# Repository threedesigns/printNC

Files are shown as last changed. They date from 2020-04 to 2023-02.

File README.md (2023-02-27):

# printNC V2.1 (outdated) Please use [printNC Wiki](https://wiki.printnc.info/en/home) for updated files and build guide. 
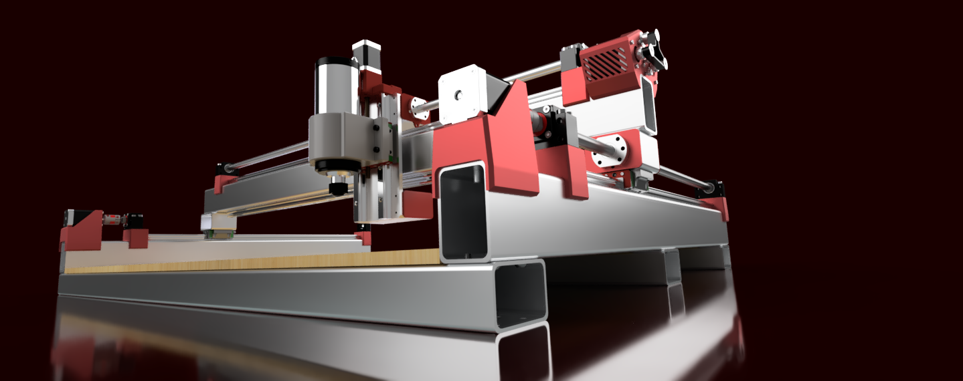
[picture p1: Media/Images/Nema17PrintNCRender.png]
printNC Logo


The PrintNC is a high-performance, DIY CNC router. It's based on a steel frame to ensure rigidity and uses 3D printed parts to make assembly easy. The PrintNC project is in active development and encourages participation.

We are looking at possibly using this repository to maintain just the models, but for now this repository should not be used.

Is there something you’re looking for that is not here yet? Join [Discord](https://discord.gg/RxzPna6) and ask there. Answers are fast and the community is quickly growing!

Additional information can also be found on the official website: [https://threedesign.store](https://threedesign.store)

## License

The PrintNC is completely open-source and operates under the CC BY 4.0 license. See the [LICENSE](LICENSE.md) file for more information.

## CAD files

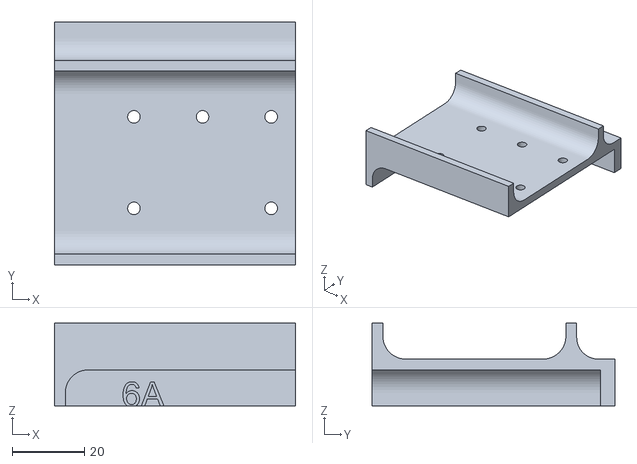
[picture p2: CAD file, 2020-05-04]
Printed Parts/Bundles/3x2x1_8 1_4 radius/Assembly Tools/6A - X Gantry Part 2.stl
66.9 x 67.4 x 23.0

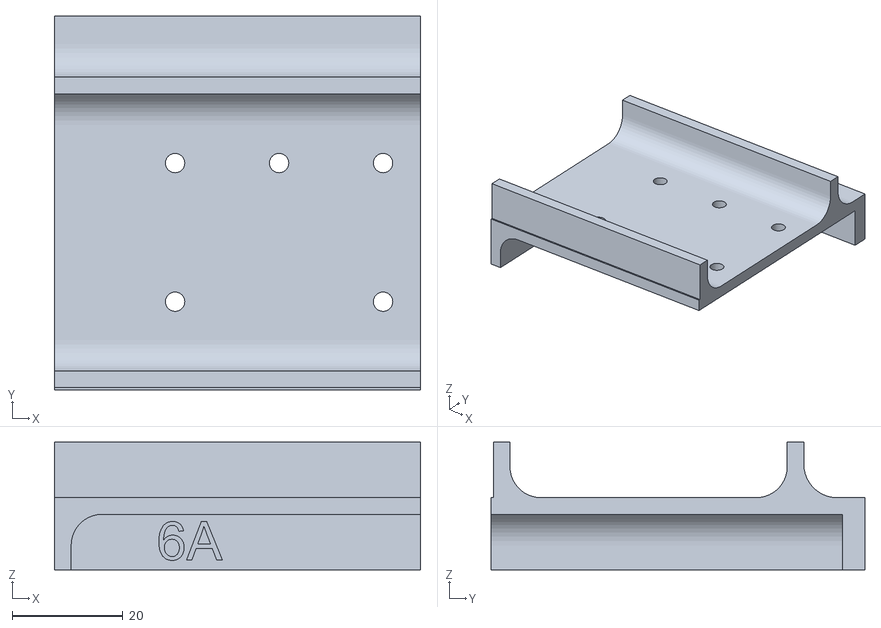
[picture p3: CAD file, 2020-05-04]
Printed Parts/Bundles/75x50x3 6mm Radius/Assembly Tools/6A - X Gantry Part 2.stl
66.0 x 67.4 x 23.0

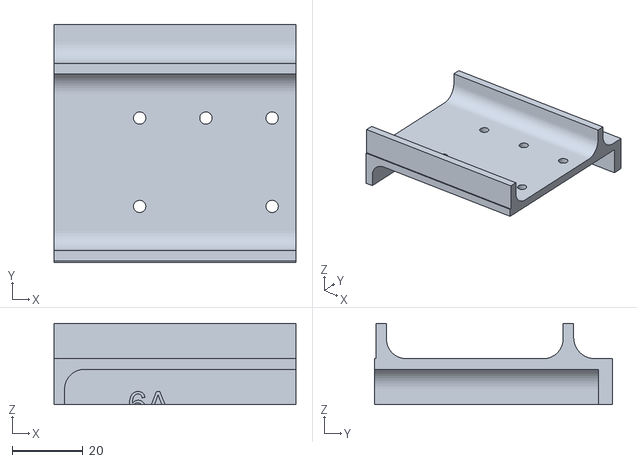
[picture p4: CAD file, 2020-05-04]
Printed Parts/Bundles/80x50x3 6mm Radius/Assembly Tools/6A - X Gantry Part 2.stl
68.5 x 67.4 x 23.0

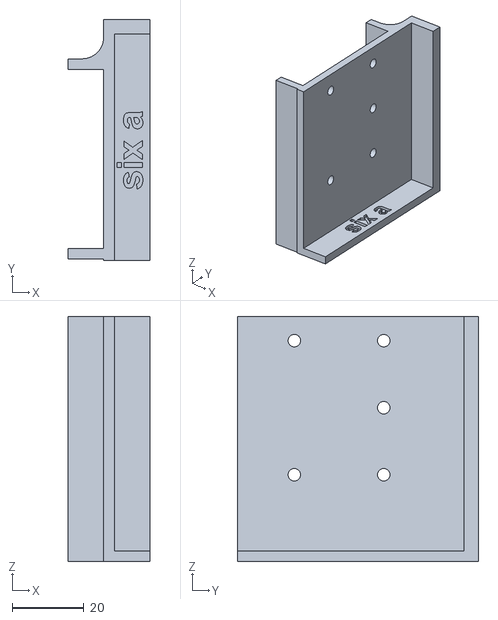
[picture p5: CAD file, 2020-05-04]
Printed Parts/Bundles/80x50x3 Square/Assembly Tools/6A - X Gantry Part 2.stl
23.0 x 67.4 x 68.5

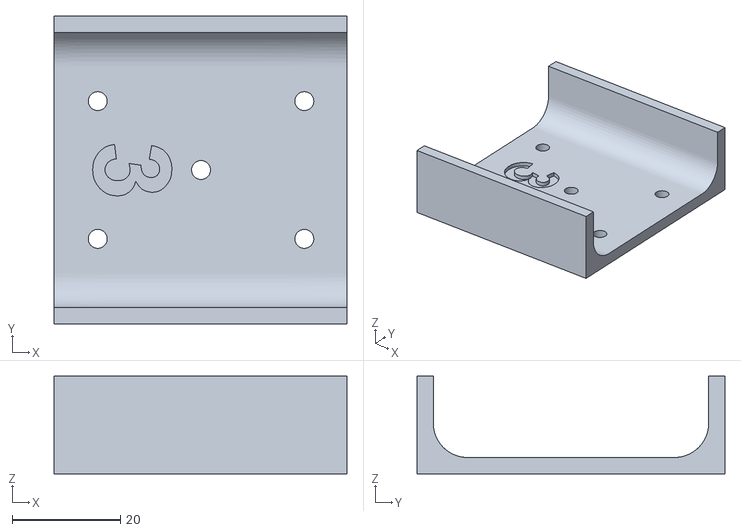
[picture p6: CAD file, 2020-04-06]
Printed Parts/Bundles/3x2x1_8 1_4 radius/Assembly Tools/3 - Y Frame Mid Marker.stl
54.0 x 56.8 x 18.0

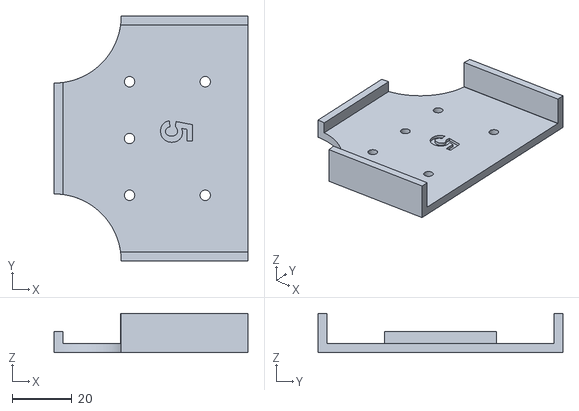
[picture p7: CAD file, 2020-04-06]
Printed Parts/Bundles/3x2x1_8 Square/Assembly Tools/5 - Y Roller Top.stl
65.0 x 82.2 x 13.1

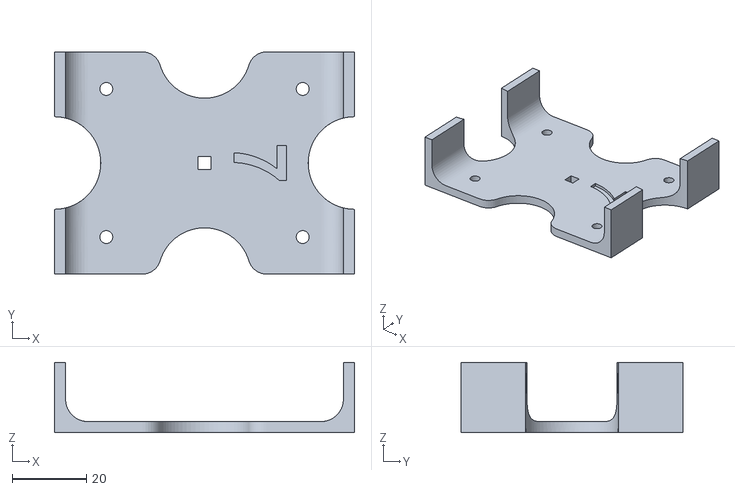
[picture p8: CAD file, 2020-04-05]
Printed Parts/Bundles/75x50x3 6mm Radius/Assembly Tools/7 - X Axis Roller.stl
81.0 x 60.0 x 19.0

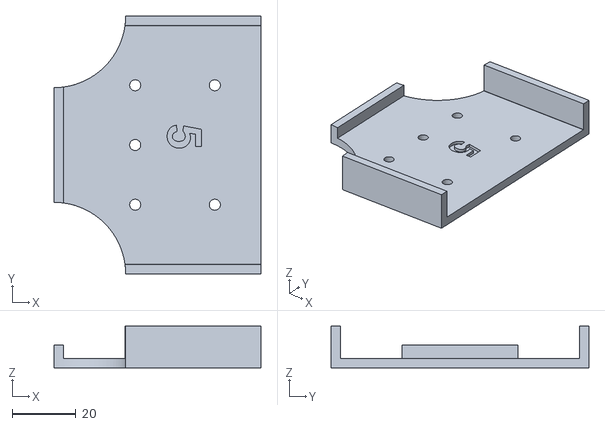
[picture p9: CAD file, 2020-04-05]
Printed Parts/Bundles/75x50x3 Square/Assembly Tools/5 - Y Roller Top.stl
65.0 x 81.0 x 13.1

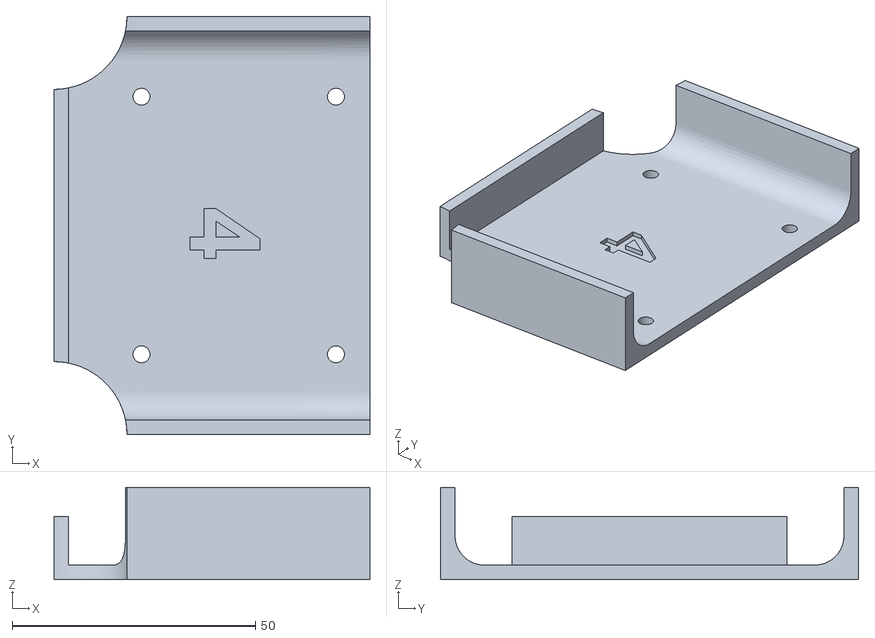
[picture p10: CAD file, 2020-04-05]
Printed Parts/Bundles/80x50x3 6mm Radius/Assembly Tools/4 - Y Roller Bottom.stl
65.0 x 86.0 x 19.0

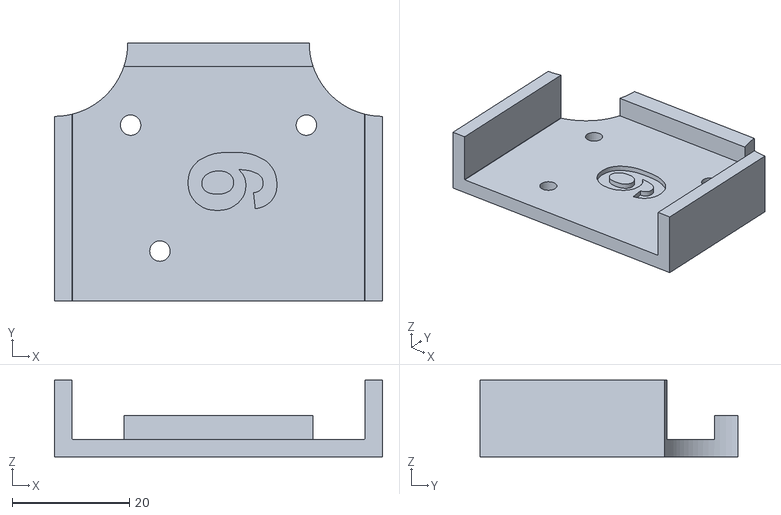
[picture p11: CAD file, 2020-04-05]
Printed Parts/Bundles/80x50x3 Square/Assembly Tools/9 - Z Face Rail Bottom.stl
56.0 x 44.0 x 13.1

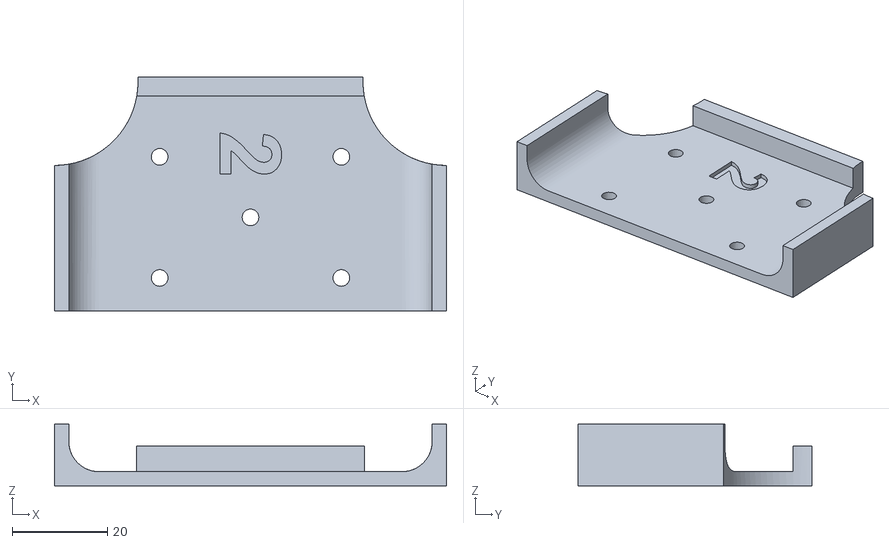
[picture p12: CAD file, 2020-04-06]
Printed Parts/Bundles/3x2x1_8 1_4 radius/Assembly Tools/2 - X Frame Marker.stl
82.2 x 49.0 x 13.0

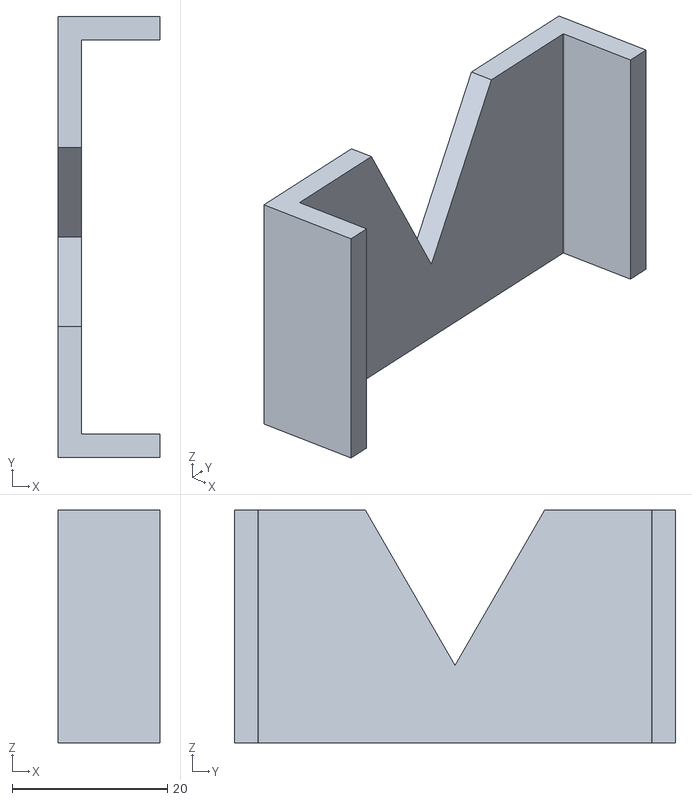
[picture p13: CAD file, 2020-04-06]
Printed Parts/Bundles/3x2x1_8 Square/Assembly Tools/Centre Line Marker.stl
13.1 x 56.8 x 30.0

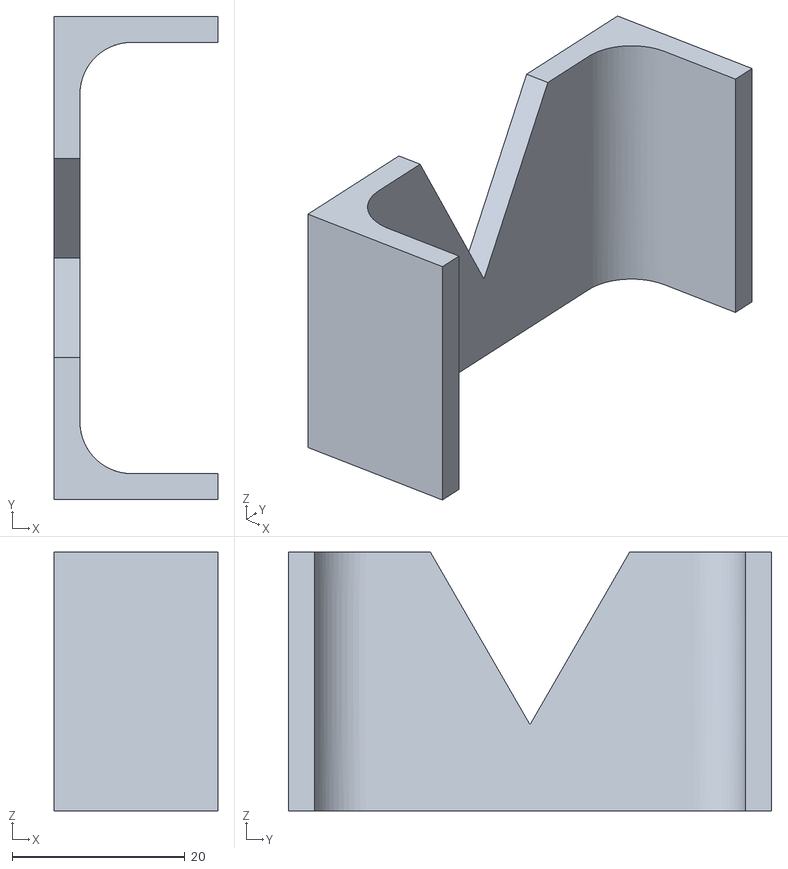
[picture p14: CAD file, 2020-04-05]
Printed Parts/Bundles/75x50x3 6mm Radius/Assembly Tools/Centre Line Marker.stl
19.0 x 56.0 x 30.0

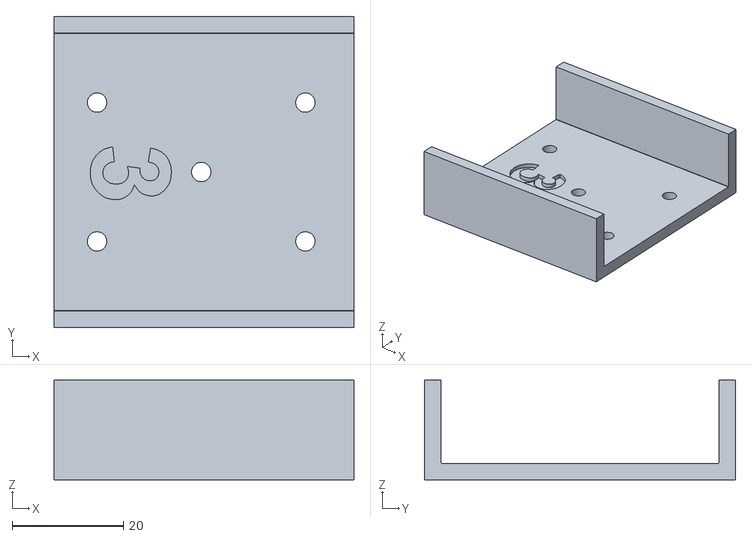
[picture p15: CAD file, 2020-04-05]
Printed Parts/Bundles/75x50x3 Square/Assembly Tools/3 - Y Frame Mid Marker.stl
54.0 x 56.0 x 18.0

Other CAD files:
Printed Parts/Bundles/3x2x1_8 Square/Assembly Tools/6A - X Gantry Part 2.stl
Printed Parts/Bundles/75x50x3 Square/Assembly Tools/6A - X Gantry Part 2.stl
Printed Parts/Bundles/80x50x3 6mm Radius/Assembly Tools/3 - Y Frame Mid Marker.stl
Printed Parts/Bundles/80x50x3 Square/Assembly Tools/1 - Y Frame Marker.stl
Printed Parts/Bundles/3x2x1_8 1_4 radius/Assembly Tools/1 - Y Frame Marker.stl
Printed Parts/Bundles/3x2x1_8 1_4 radius/Assembly Tools/4 - Y Roller Bottom.stl
Printed Parts/Bundles/3x2x1_8 1_4 radius/Assembly Tools/5 - Y Roller Top.stl
Printed Parts/Bundles/3x2x1_8 1_4 radius/Assembly Tools/6 - X Gantry.stl
Printed Parts/Bundles/3x2x1_8 1_4 radius/Assembly Tools/7 - X Axis Roller.stl
Printed Parts/Bundles/3x2x1_8 1_4 radius/Assembly Tools/8 - Z Face Rail Top.stl
Printed Parts/Bundles/3x2x1_8 1_4 radius/Assembly Tools/9 - Z Face Rail Bottom.stl
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

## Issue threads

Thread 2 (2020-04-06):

BOM state to use M6, but hole are sized for M5.

excessnet, 2020-04-06:
Hole on BK/BF12 are 5.8mm (M5 "loose fit"), but the BOM recommand to use M6x30.

We sould either update the BOM to M5 or modifity the part to have a 6.6~6.8mm hole.

I will use M5x35mm on mine.

excessnet, 2020-04-06:
Talked a little on Discord and I need to add those comments.
- This was by design... Hoges wanted let the M6 thread into the plastic to make sur it's a tight fit so it dosent introduce backlash.

M5 are actually loose, since 5.8 it's "loose fit", "tight fit" would be 5.3.. or 5.5 for "normal" fit.

Hole should be around 6.4 for M6 "tight fit".

If you thread the M6 into the plastic, it won't "pull" the part, so it might not touch the tubing correctly.

I feel like you need a "loose fit" so you can align thing correctly, but that could introcude backlash... so maybe we should just add a layer of double side tape on the tubing, so when it's all tighted down, it will stick there and won't be able to move?

I will try with M5 first, since I do have them and I can upgrade to M6 later if needed.

BiuTse, 2020-04-06:
We will Redesign the part for V1.1

jaymis, 2020-05-04:
Pretty sure this is actually working as designed with M6? Has anyone commenting here actually built this section of the machine?
When you first screw in the M6 screws they tap a thread into that part, and then they're very tight fitting. There is some play to correctly align the mount block, but when screwed down tightly it's very solid.

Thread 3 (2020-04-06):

Z-Axis NEMA 23 Mount.stl on Zip on Main Page don't have the Mounthing Hole

excessnet, 2020-04-06:
The "Z-Axis NEMA 23 Mount.stl" on the ZIP is using the wrong version.

I suggest removing any download files from the webpage and redirect people here where fille will be up to date.

BiuTse, 2020-04-06:
For which beam Dimension?

excessnet, 2020-04-06:
Was for the 2x3

BiuTse, 2020-04-06:
ok thx.
Asked Hoges if he could provide the right files.

BiuTse, 2020-04-08:
Here in this project the files are now correct. But on the Homepage they are still wrong.
Will close the issue, when it's also done on the main page

BiuTse, 2020-05-01:
Hoges fixed files

excessnet, 2020-05-01:
don't fix it, remove completely and point to the file here !

Closed 2020-05-01.

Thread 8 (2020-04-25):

Add unique X axis Ball Screw Face Plate to 3d printing STL collections

MoosenElch, 2020-04-25:
The X axis has a ball screw face plate with an additional tab to mount the endstop bolt to. The existing collection of different sized STL's does not contain an stl for this part

BiuTse, 2020-04-30:
Solved

Closed 2020-04-30.

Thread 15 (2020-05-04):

Add spacer plate to BoM for Nema 23 Z Axis

jaymis, 2020-05-04:
If you're using a Nema 23 motor on the Z axis, you need a spacer plate underneath the spindle mount, so the spindle clears the Z motor mount.

https://discordapp.com/channels/648972213734604807/648972213734604810/683188554351771674

https://discordapp.com/channels/648972213734604807/648972213734604810/706944254987075694

An elegant solution may be a design that could be printed and then replaced with a machined aluminium part, or otherwise a template/hole drilling pattern so people can fabricate their own from aluminium plate.

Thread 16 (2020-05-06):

Add a "decide on how you'd like to attach your wasteboard and drill holes" step to the assembly guide?

jaymis, 2020-05-06:
> Wasteboard is something I've been thinking should be expanded upon a little in the build guide. I know there's a couple of holes there, but my plan is to have a bunch of evenly spaced threaded holes so I can experiment with some different wasteboard options.
>
> Unfortunately I'm going to have to partially disassemble the machine to drill those holes with my drill press, so it might be worth adding a "think about your wasteboard/holding situation now, before assembling the frame" step into the build

https://discordapp.com/channels/648972213734604807/648972213734604810/707396155746680973

excessnet, 2020-05-06:
I think the best way is to have something as a "floor" (MDF, hardwood or whatever you want) that cover the whole "floor" area of the CNC.

On top of that, you add an MDF wasteboard, glued to the "floor". This one will only be the working area (you can even make a program to cut the contour perfectly). You will surface this wastboard with the CNC and can also create hole or whatever you want in it. When it has been surfaced a lot, you can just glue another one on top of it and surface it again (just keep the program and run it again)! :)

The reason for that is that you can have part that will be larger than what the CNC can reach (working area) and if your surface the board, you'll endup with a "higher" concour than then working area. It will then be impossible to level what you place on the surface.

My english is not very good... I hope I made myself clear! :(

excessnet, 2020-05-06:
as for holding, on my MPCNC, I made some dog hole, I could just put some copper pipe tight in them so I can align the stock I was placing straight (since the CNC did the hole, it was straight to itself).

I then used some lever-clamp DIY (can't remember where I find those), but I like the idea of Marius Hornberger using t-slots.

justinclift, 2020-05-06:
> On top of that, you add an MDF wasteboard, glued to the "floor".

@excessnet Glue (eg [this](https://en.wikipedia.org/wiki/Adhesive)) is probably not the right approach, because it would be hard to remove the MDF afterwards.  Using nuts and bolts to hold down the wasteboard though is common.

excessnet, 2020-05-06:
you don't remove it, just surface it until it's too small or there's nothing left, then stick another one on top.

I tried bolts, but you need many to keep the wasteboard straight and you risk hitting them when surfacing when it's starting to be too thin.

jaymis, 2020-05-06:
I guess because a wasteboard is something that will be depending on how a person utilises their machine, we can approach it more as "here are some options that work well" rather than "this is the way to do your wasteboard".
I think the most important thing is that people should try to make a decision on the wasteboard/fixture system before assembling the frame, and that's not really mentioned in the build docs at the moment.

justinclift, 2020-05-06:
Good point @jaymis. :smile:

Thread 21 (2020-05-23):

Fusio360 File - guides are broken if tube > 90mm

BiuTse, 2020-05-23:
Using a 100x50mm (or 90x50mm) parameter in the Fusion360 File will generate wrong guides

Closed 2020-05-29.

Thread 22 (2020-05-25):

BOM is missing M6x20 Screws for 70mm tubing to hgr20 carriage

Conversage, 2020-05-25:

giesberge, 2020-05-25:
I think I just use the 15mm there. I'm not sure why there are inconsistencies between build guide and BoM.

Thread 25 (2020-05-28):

Bill of Material lists 5/16" threaded rod, change to 10-24 threaded rod to equal 5mm

LoganFraser, 2020-05-28:
Bill of Materials lists the following:

M5X100 | 12 | May be substituted for M5 or 5/16 Threaded Rod | x | x | Ballscrew Block (Y Axis)

5/16" is equal to ~8mm and much too large for the 5.5m holes in the leadscrew nut.

5mm is 0.19", and so is 10-24 threaded rod, so for imperial builds, 10-24 rod or bolts and nyloc nuts can be used instead.

Closed 2020-09-21.

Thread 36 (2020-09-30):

What items would you like to see in the github repo vs the wiki and vs the website?

giesberge, 2020-09-30:

JoshuaGranger, 2020-10-02:
I did some research and I see that we _can_ make version-specific pages on the Wiki. However, I am concerned that we cannot create issues/pull requests on Wiki articles. IMO that's a good reason to do most of the documentation in the Documentation folder. This is a good read: https://stackoverflow.com/questions/10642928/how-to-pull-request-a-wiki-page-on-github

JoshuaGranger, 2020-10-02:
As far as what information to show on the website: I think the website should have promo information (pictures, videos), the frame-size calculator, and a link to Discord/Github.

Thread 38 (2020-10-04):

Holes on v2.1 Z Bottom Plate are flipped

natewalck, 2020-10-04:
In the CAD model for the v2.1 Z (I believe mine is current, if it isn't, please disregard), the holes for the bottom plate appear to be flipped.

The holes for mounting to the main Z plate should be tapped M5 holes and the holes for mounting the W20C carriage should by M6.5 untapped holes.

Here are the holes in question:

Plate mounting holes:

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

W20C mounting holes:

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

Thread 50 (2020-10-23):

Z2.1 Missing End Stop Switch System

NeoKurtex, 2020-10-23:
The Z2.1 file does not include any place for an endstop switch. The file should be updated to include one, especially now that the ballscrew mod is shipped with the kit. There are mods on the discord that can make this a plug-and-play fix.

(I'd also suggest making the X tramming plates visible to reduce confusion)

[https://myhub.autodesk360.com/ue2ce8530/g/shares/SH56a43QTfd62c1cd968c3fbce0791e3d1ba](url)

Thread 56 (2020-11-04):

Remove Wiki

NeoKurtex, 2020-11-04:
In efforts to streamline documentation, I would like to remove the github wiki pages and link to the wikijs site we are building. Any concerns?

[https://wiki.printnc.info/en/home](https://wiki.printnc.info/en/home)

LoganFraser, 2020-11-04:
That seems reasonable to me. I think the wiki here is hard to find for many people. Having it linked from the main github page would help that, but if the new one is easier to design and contribute to, I'm all for it.

NeoKurtex, 2020-11-04:
The new wiki should be much easier to work with. It allows for Discord and site-specific logins, has a WYSIWYG editor, and has local image hosting.

The only barrier to get started is obtaining 'contributor' status. Anyone who has made an account thus far is already a contributor.

If you would like to contribute but have not yet made an account, that's the first step.
From there, we can edit your privileges.

This wiki should be gone by this weekend unless anyone has any hesitations.

jaymis, 2020-11-04:
Maybe wait until the external wiki has at least some level of content organisation? It seems pretty bare at the moment, unless there's something I'm missing? The current wiki home page has at least a good starting point: https://github.com/threedesigns/printNC/wiki

Whereas the new one has "test test" https://wiki.printnc.info/en/home

LoganFraser, 2020-11-04:
Also:

Drivers
Drivers!
asdasdasdasd

NeoKurtex, 2020-11-05:
Everything is already in the wiki, the pages just need to be added to the navigation bar.. should take me a few minutes

NeoKurtex, 2020-11-15:
File contents are now fully migrated

Closed 2020-11-15.

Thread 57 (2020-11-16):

Regarding Bundles

NeoKurtex, 2020-11-16:
Bundles are out of date as of V2.1. In addition, I feel like they are not a good idea. As we have come to learn, tube radius can have significant tolerance allowances. I suggest either
1) archive the files or
2) update for V2.1 with guaranteed safe tolerances (close to square for extern parts and large radius for internal parts)

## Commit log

2020-04-01 Differenciated the needed # of drivers for Nema17/23
2020-04-06 Face Plate for 80x50 Profile
2020-04-06 Delete PrintNC Face Plate 80x50 v1.pdf
    Wrong Folder
2020-04-08 renaming 3dprint to src
    [1 - Y Frame Marker.stl, 2 - X Frame Marker.stl, 3 - Y Frame Mid Marker.stl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]
2020-04-27 changing folder name
    [1 - Y Frame Marker.stl, 2 - X Frame Marker.stl, 3 - Y Frame Mid Marker.stl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]
2020-04-27 Initial commit for implementation of Fusion 360 scripts including STL generation script.
2020-04-27 Fix unit issue and faceplate endstop output
2020-04-27 Endstop faceplates added
    [Ball Screw Face Plate w EndStop.stl]
2020-04-27 Fix 3x2 Radius issue in script and endplate
    [Ball Screw Face Plate w EndStop.stl]
2020-04-30 Added descriptions to BoM for Dual NEMA17 mount.
2020-05-02 Hoges removed extra fillet preventing 6A from properly mating with Y-roller.
    [6A - X Gantry Part 2.stl]
2020-05-03 Added fillets back to radius'd profiles
    [6A - X Gantry Part 2.stl]
2020-05-08 allow M6x16mm, add head types, added 4.2mm drill
2020-05-13 Added T-track image
    image provided by BiuTse
2020-09-07 Update bom.md
    corrected 5/16 to 10-24 threaded rod (Issue 25)
2020-09-20 Tool for checking Steel tubing radius.
    [CornerRadiusTool.f3d]
2020-09-20 Create This is for Assembly and Milling Tools
2020-09-20 Steel tubing corner radius tool.
    [CornerRadiusTool.f3d]
2020-09-21 Created Tools directory and added corner radius tool (#31)
    [CornerRadiusTool.f3d]
2020-09-22 Fixed issue with design.
    [RadiusTool.f3d]
2020-09-22 Update This is for Assembly and Milling Tools
2020-09-23 Delete CornerRadiusTool.f3d
    Incomplete F360 design, delete.
    [CornerRadiusTool.f3d]
2020-10-02 Add files via upload
    Used for centering the linear rails on the steel tube while drilling and assembling. For Y2 only, after assembling and squaring the frame and installing the X gantry, loosen the Y2 linear rail screws and use the gantry to align the y2 linear rail to the Y1 and retighten as you slide the gantry along.
    [Linear Rail Center Guide v9.f3d]
2020-10-02 Drastic reorganization
    No files deleted -- only reorganized.
    [1 - Y Frame Marker.stl, 2 - X Frame Marker.stl, 3 - Y Frame Mid Marker.stl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]
2020-10-02 Revert "Drastic reorganization"
    This reverts commit 9b858ff2eb0330439da31a5410a71328510894e3.
    [1 - Y Frame Marker.stl, 2 - X Frame Marker.stl, 3 - Y Frame Mid Marker.stl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]
2020-10-04 Modernization Effort (#37)
    * Reorganization
    Reorganized and added assembly tools
    * Update README.md
    Trying to fix README links
    * Update README.md
    * Update README.md
    * Update drilling_guides.md
    * Update drilling_guides.md
    * Update drilling_guides.md
    * Update drilling_guides.md
    * Update endstop_wiring.md
    * Update faq.md
    * Update vfd_config.md
    * Update electronics.md
    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
    [1 - Y Frame Marker.f3d, 1 - Y Frame Marker.stl, 2 - X Frame Marker.f3d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]
2020-10-06 Added two new community tools (#39)
    * Added Spindle Drill Jig by @rcw#0895
    * Renamed Spindle Mount for clarity
    * Added the M5 cutting jig from @gerrg#7760
    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
    [M5_threaded_Rod_cutting_Jig_-_164.5mm.stl, spindle-drill-jig.fcstd, spindle-mount-drill-jig-back.stl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]
2020-10-06 Modifications to Rail Centering Jig (#40)
    * Linear Rail Center Guide modifications
    Added folder for Linear Rail Center Guide with a README and added Jake's rendition
    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
    [Linear Rail Center Guide v9.f3d, Railguide.SLDPRT]
2020-10-06 Updated Logan's Rail Center Guide
    [Linear Rail Center Guide v9.f3d, Linear_Rail_Center_Guide_v2.f3d]
2020-10-06 Replaced NEMA23 with Logan's latest version
    [NEMA23.f3d, Nema23_Motor_Mounts_v4.f3d]
2020-10-06 Updated Spindle Mount Drill Jig README
2020-10-06 Adding VFD and spindle information (#44)
2020-10-06 Add files via upload
    Radius Tool for radius 9mm - 12mm
    [RadiusTool 9-12 v2.f3d]
2020-10-06 Spindle Configuration (#45)
    Added spindle document from website and moved it into a folder with m0jo's guide
2020-10-06 Organizing Spindle Configuration (#47)
    * Spindle Configuration
    * Getting up to date from Master (#46)
    * Adding VFD and spindle information (#44)
    * Add files via upload
    * Spindle Configuration (#45)
    * Removing extra readme and organizing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
2020-10-24 Cleaning up 3D Printed Parts (#51)
    Added proper BK15/BF15 parts. Modified BK15/BF15 with endstop mods so they have correct dimensions. Renamed a few files for uniformity.
    [2010 Ballscrew Plates.f3d, BF15 Endstop Mod.f3z, BF15 Mount.f3d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]
2020-10-24 Added Logan's V2 Motor Mount
    [NEMA23 Motor Mount V2.0.f3d]
2020-10-28 Logan's Keyhole Plates (#55)
    [BallScrewKeyholeFacePlate.f3d]
2021-01-05 Aluminum Z motor mount
    [Z_motor_alu_mount.step, Z_motor_alu_mount_ME-8111_limit_switch_mount.step]
2021-02-01 Removed old data
    [1 - Y Frame Marker.stl, 2 - X Frame Marker.stl, 2010 Ballscrew Plates.f3d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]
2021-02-01 assembly tools readded
    [1 - Y Frame Marker.stl, 2 - X Frame Marker.stl, 3 - Y Frame Mid Marker.stl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]
